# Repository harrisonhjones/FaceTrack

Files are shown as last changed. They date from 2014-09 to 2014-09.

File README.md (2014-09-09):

# FaceTrack
Banner
A visual servoing example using SimpleCV and an Arduino. 

## Motivation
The motivation behind this project came from the desire to implement visual servoing in the real world in an application I would actually use. While I don't do it often enough I occasionally video chat with my parents. When video chatting the camera position and viewport is static and usually I end up fiddling with it until it's roughly pointing at my face during the chat. If I moved around I would fall out of frame. I know some higher-end web cameras have facial tracking built into them but I never could justify the expense when it looked like something easy to implement. It turns out I was right, it's pretty easy to do!

## How It Works
This project has three core "parts". The Hardware consists of a DIY pan/tilt webcamera controlled by an arduino. The firmware simply listens for desired servo positions over the serial port and sends those to the attached servoss. The software is where the magic happens. Using a [Haar Cascade](http://simplecv.sourceforge.net/doc/cookbook.html) faces infront of the camera are recognized, facial offsets are calculated, and new servo positions are sent to the arduino over serial. The final result is a camera setup which follows your face! 

## Bill of Materials/Software
### Hardware
You need the following physical items

* A webcamera of some kind. Any usb web camera should work. I used a [Microsoft Lifecam Studio](http://www.microsoft.com/hardware/en-us/p/lifecam-studio).
* Two standard [servos](https://www.sparkfun.com/products/11884)
* Custom 3D printed pan/tilt fixture. See below for my design
* Microcontroller / Arduino. I used an Arduino Uno and my firmware is for an Uno. You may have to adapt it for your microcontroller
* Hot Glue / Adhesive Strips

### Firmware
If you are using an Arduino UNO you simply need to download the firmware (found in the "firmware" folder in the source code respository or directly [here](http://hhj.me/facetrackfirmware)) and open it using the [Arduino IDE](http://arduino.cc/en/main/software)

### Software
You need to have the following software installed

* [Python 2.7.x](https://www.python.org/download)
* [SimpleCV (A python OpenCV Wrapper)](http://simplecv.org/download)
* [pySerial](http://pyserial.sourceforge.net/pyserial.html#installation)
* A "camera splitter" if you are on Windows (perhaps other OSes as well). I've been using [ManyCam](http://manycam.com/) but I'd love to find something open source

## Running the FaceTracker
### Hardware
To get the hardware preparred for firmware and software follow the following steps.

* Assemble the custom 3D printed pan/tilt fixture. 
* Install both servos in the fixture
* Attach the servo horns to the fixtures using an adhesive. I prefer high-strengh hot glue
* Attach the fixture to your wall/monitor using an adhesive. Hot glue will work but I prefer adhesive velcro strips
* Plug the yaw servo into the Arduino. Red goes to 5V. Black goes to GND. Yellow/Brown/Signal goes to Digital Pin 9
* Plug the pitch servo into the Arduino. Red goes to 5V. Black goes to GND. Yellow/Brown/Signal goes to Digital Pin 8

### Firmware
Simply upload the Firmware.ino file to the Arduino. Open up the Serial Monitor once the upload is complete. You should see the following.

    #System Start
    $Version:1.0
    !Timeout
    !Timeout
    !Timeout
    ... (more "!Timeout")

Make a note of what serial port your arduino is on.

### Software
Open FaceTrack.py in your favorite text editor and look at for the following line

    ser = serial.Serial('COM4', 9600, timeout=1)

You want to change the serial port definition to match your setup. Change 'COM4' to match what serial port your arduino is on. 

With that change save the file and run it. If all goes well you should see your camera's viewport in a window. Once you stick your face in the view plane a red box should be drawn around it and the camera should move to bring your face toward the center of the viewport. Move around, it should follow you!

## Serial Protocol
The serial protocol is very simple. The protocol to the Arduino is fairly straight forward: ">YYYPPP\n" where YYY and PPP are zero padded numbers representing Yaw and Pitch servo positions respectively. The protocol back from the Arduino is a little more interesting. The valid formats are as follows

* #CommentGoesHere\n
* $VariableName:VariableValue\n
* !EventName\n

### Comments
Comments can be anything. They are really for debugging purposely only

### Variables
Variable names can be pretty much anything. Currently used variables are:

* Version - The firmware version number
* YawValue - The current yaw servo value
* PitchValue - The current pitch servo value

### Events
Events can be anything but only the following 3 are used/supported:

* Timeout - Indicates that the camera hasn't gotten any information for 1 second
* ACK - The last command is valid and acknowledged
* NAK - the last command is not valid

## Debugging
The biggest problems you might encounter is that every servo is different and because of that you may need to edit the software to match your setup. 

### The Camera Moves Away from my Face
If this happens you simply need to edit FaceTrack.py. Open it up and look for the following lines

    if (xErr < xErrMin):
        yawDelta = -1
    elif (xErr > xErrMax):
        yawDelta = 1
    else:
        yawDelta = 0

    if (yErr < yErrMin):
        pitchDelta = 1
    elif (yErr > yErrMax):
        pitchDelta = -1
    else:
        pitchDelta = 0

If the yaw servo is moving in the wrong direction swap the lines which read

    yawDelta = -1

and 

    yawDelta = 1

If the pitch servo is moving in the wrong direction swap the similar pitch servo lines

### The Camera "Centers" on the Wrong Spot. 
This is also an easy fix. Open up FaceTrack.py and edit the following lines near the top

    # Default positions for the yaw and pitch servos. Change these numbers to match your setup
    yawPos = 100
    pitchPos = 107

### The Camera Doesn't Move Far Enough to Either Side
Again, an easy fix. Open FaceTrack.py and edit the following lines

    if (yawPos < 30):
        yawPos = 30
    if (yawPos > 150):
        yawPos = 150
    if (pitchPos < 50):
        pitchPos = 50
    if (pitchPos > 130):
        pitchPos = 130

Change these limits to match your setup

### The Camera Oscillates or Lags Too Far Behind the Face
Open FaceTrack.py and edit the following lines

    # Tolerances. Tighter tolerances (smaller) track the face more percisel but result in move movement. If the tolerance is too small the camera might begin to oscillate.
    xErrMin = -10;
    xErrMax = 10;
    yErrMin = -10;
    yErrMax = 10;

## Custom Pan/Tilt Hardware
These part files were modeled given the following design requirements

* Mount onto a wall. The large flat on the back of the yaw servo holder is for adhesive velcro strips
* Hold two standard servos
* Semi-universally hold a web camera. Should hold onto any cylindrical or spherical camera. Made to specifically hold a Microsoft Lifecam Studio
* Be 3D printable without support material/structure. Overhangs > 45 degrees and holes not along the Z-axis should be avoided.

### Render
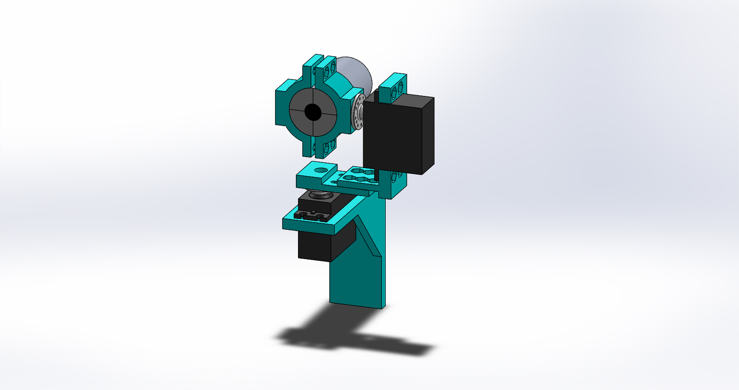
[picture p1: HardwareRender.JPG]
Render of the custom 3D printed hardware


### Model Files
Model Files can be found in the "Hardware" folder. STLs ready for 3D printing can be found in the "STLs" subfolder

## Videos/Pictures
Unfortunately I don't have any videos or pictures of this thing running. I finished this project a while back and have since needed the servos for other projects. I will try to rebuild it and take a video / pictures as soon as I find time

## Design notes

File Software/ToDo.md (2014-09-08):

#To Do

## Keyboard Commands

* Allow for tracking to be "paused" and "resumed" via keyboard (p)

* Allow for the current face to be selected via keyboard input (space for jump :P ). So, if it is currently tracking the most centered face, a spacebar press will make it jump to tracking the second face until the second face is lost and then it will track the first face

## Facial Persistance

* When given 2+ faces do not just blindly use the first face, use whatever face is closest to the last first face. Hopefully this will mitigate the persistance problem

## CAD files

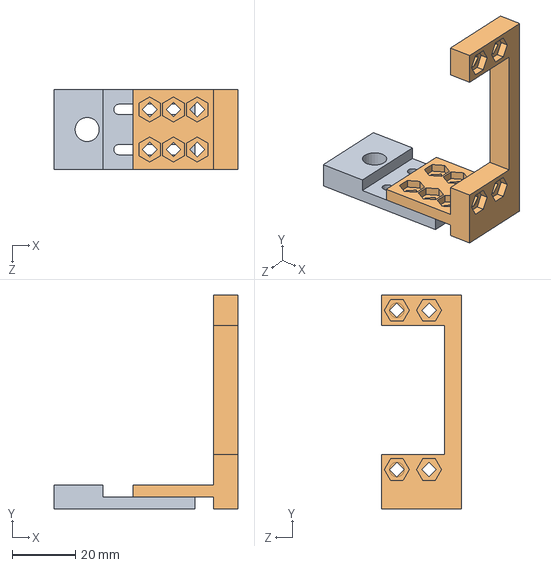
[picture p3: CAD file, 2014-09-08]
Hardware/YawArmAssembly.SLDASM
58.0 x 67.6 x 25.4 mm
YawArm-YawServoAttachment
YawArm-PitchServoAttachment

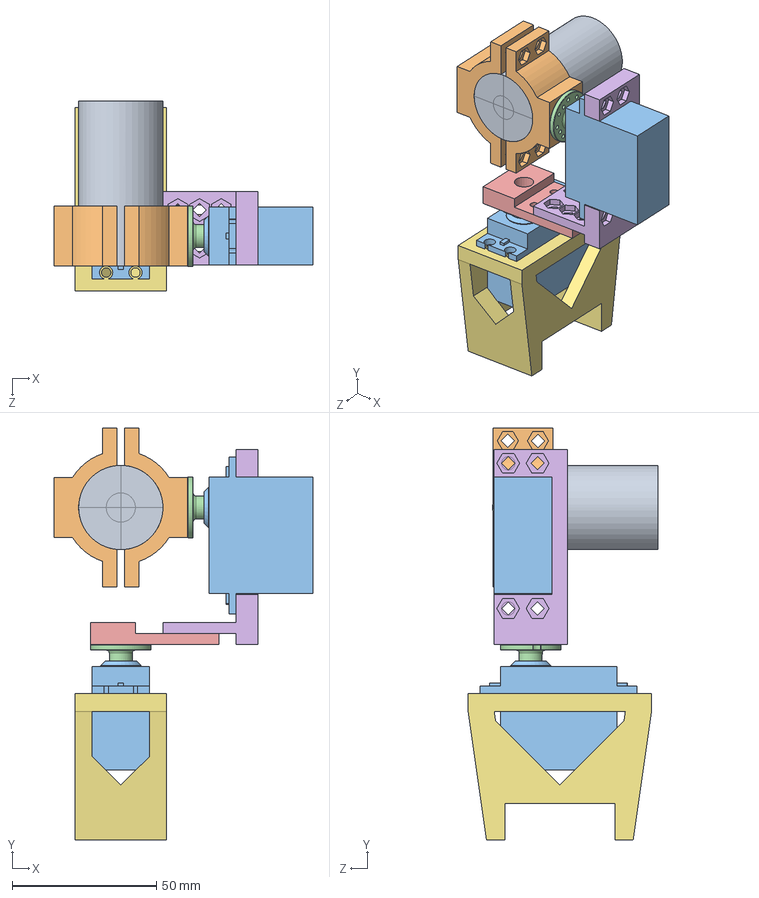
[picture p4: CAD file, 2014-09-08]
Hardware/CompleteAssembly.SLDASM
89.5 x 142.6 x 65.7 mm
Microsoft Lifecam
CameraHolder x 2
S3151 x 2
servohorn x 2
YawArm-YawServoAttachment
YawArm-PitchServoAttachment
WallPlate

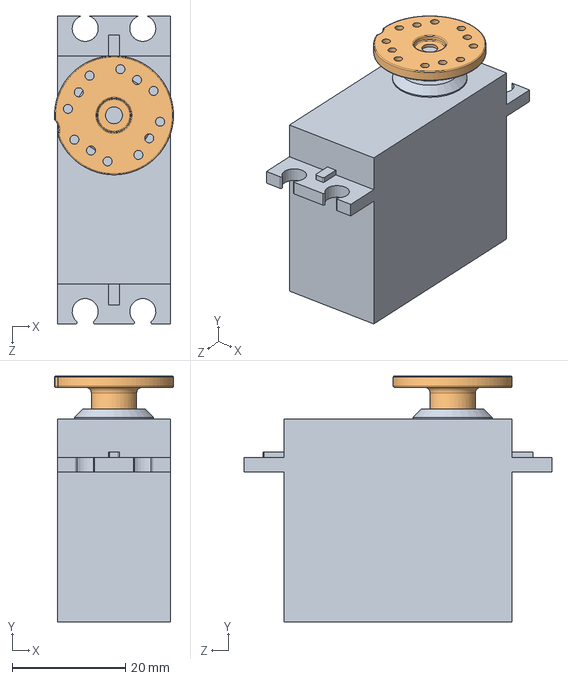
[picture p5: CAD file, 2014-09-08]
Hardware/ServoAssembly.SLDASM
21.0 x 43.4 x 54.3 mm
S3151
servohorn

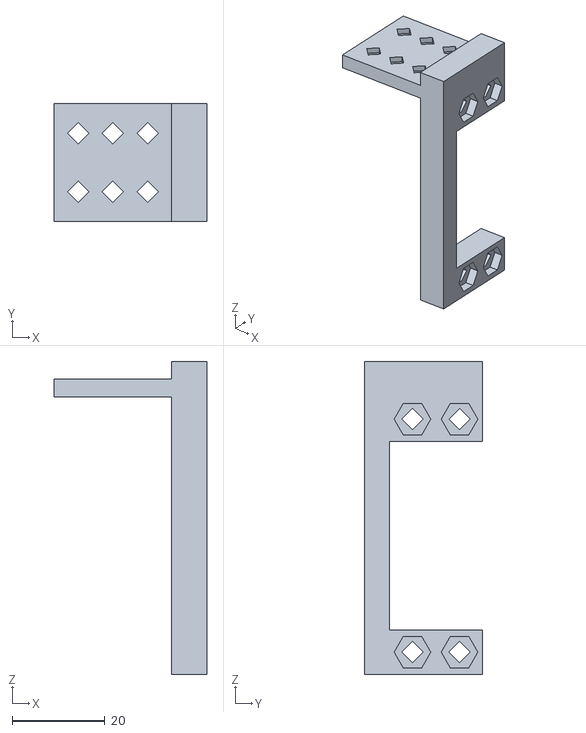
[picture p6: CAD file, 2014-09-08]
Hardware/STLs/PitchServoAttachment.STL
33.0 x 25.4 x 67.6

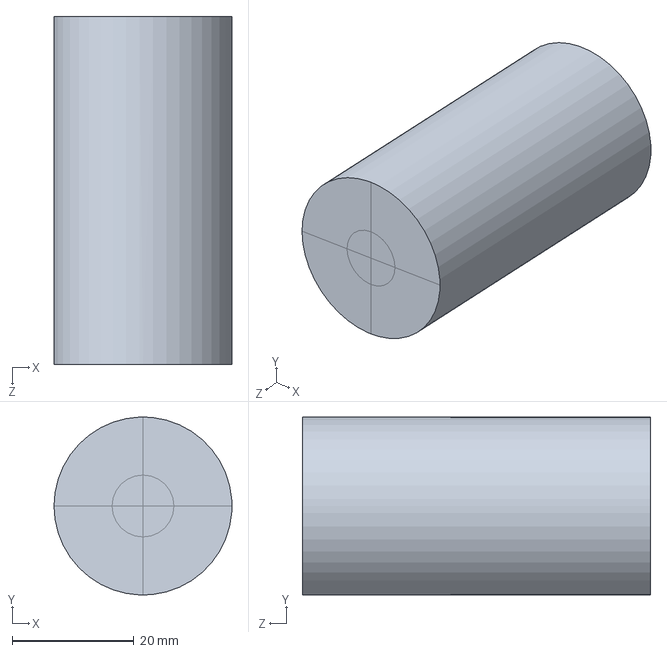
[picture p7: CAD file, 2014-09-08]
Hardware/Microsoft Lifecam.SLDPRT
29.2 x 29.2 x 57.1 mm

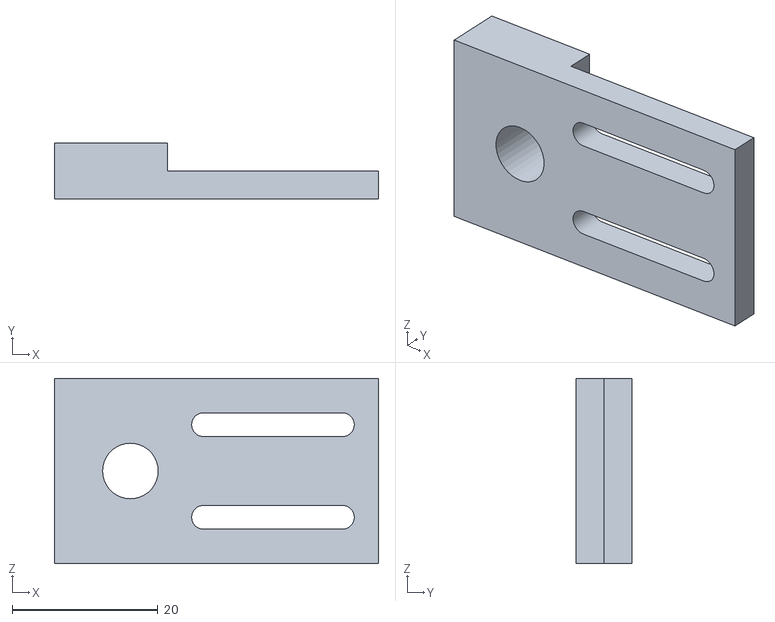
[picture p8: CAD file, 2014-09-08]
Hardware/STLs/YawServoAttachment.STL
44.5 x 7.62 x 25.4

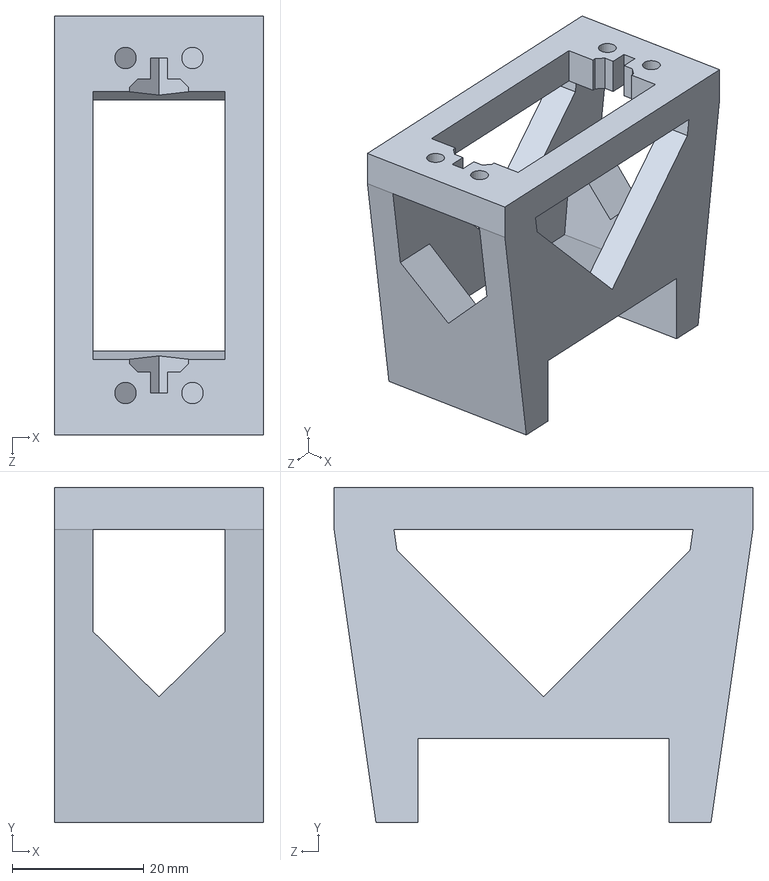
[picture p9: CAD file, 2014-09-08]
Hardware/WallPlate.SLDPRT
31.8 x 50.8 x 63.5 mm

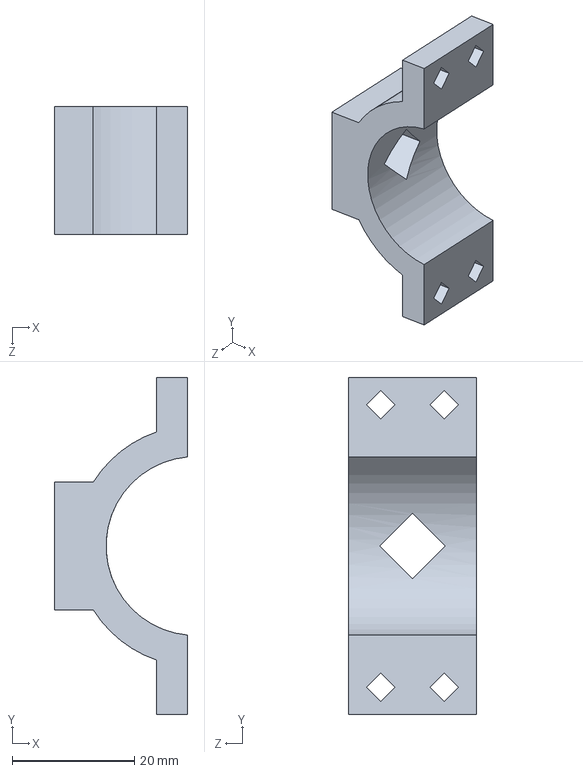
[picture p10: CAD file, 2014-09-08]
Hardware/CameraHolder.SLDPRT
21.8 x 55.0 x 20.8 mm

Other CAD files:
Hardware/YawArm-PitchServoAttachment.SLDPRT
Hardware/YawArm-YawServoAttachment.SLDPRT
Hardware/STLs/CameraHolder.STL
Hardware/STLs/WallPlate.STL

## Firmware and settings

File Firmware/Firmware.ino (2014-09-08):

// Includes
#include <Servo.h>

byte state = 0;                          // The current state. States are: 0 - waiting for start, 1-3 - waiting for yaw, 4-6 - waiting for pitch
unsigned long lastCommandTime;           // A variable to hold the last time a command was received over the serial line. Used to detect if a "timeout" has occured

String yawValue = "";                    // Two strings to hold the desired incoming (over serial) yaw and pitch values
String pitchValue = "";

Servo SRV_YAW;                          // Two servo objects. We need one for each controlled servo
Servo SRV_PITCH;

void setup() {
  Serial.begin(9600);			// opens serial port, sets data rate to 9600 bps
  
  SRV_YAW.attach(9);			// Attaches the yaw servo to pin 9
  SRV_PITCH.attach(8);			// Attaches the pitch servo to pin 10
  
  SRV_YAW.write(90);                    // Centers the yaw servo
  SRV_PITCH.write(90);                  // Centers the pitch servo
  
  Serial.println("#System Start");      // Output a comment (#) letting the user/program know the program has started
  Serial.println("$Version:1.0");       // Output a variable ($) letting the user/program know the firmware version number
}

void loop() {
  // Check for the timeout condition. If a timout has occured reset the state and let the user/program know of the event (!)
  if(millis() > lastCommandTime + 1000)
  {
    state = 0;
    Serial.println("!Timeout");
    lastCommandTime = millis();
  }
  
  // Processing incoming serial commands while we still have incoming bytes to process
  while (Serial.available() > 0) {
    lastCommandTime = millis();          // Reset the timeout clock
    int inChar = Serial.read();          // Pop a byte off of the incoming serial queue
    Serial.print("$State:");             // Debug the current state. Send it as a variable ($)
    Serial.println(state,DEC);
    if((state == 0) && (inChar == '>'))  // State the state machine. Looking for the first character ">"
    {
      state++;
    }
    else if((state > 0) && (state < 4))  // The next section of the state machine. Looking for yawValues. Builds up the yawValue string with incoming characters for later processing
    {
      yawValue += (char)inChar; 
      state++;
    }
    else if((state > 3) && (state <= 6))
    {
      pitchValue += (char)inChar; 
      state++;
    }
    else if (state > 6)                  // The end of the state machine. Outputs the yaw and pitch values and sends them to the servos
    {
      state = 0;  
      SRV_YAW.write(yawValue.toInt());                    // Send the desired yaw value to the yaw servo
      SRV_PITCH.write(pitchValue.toInt();                  // Send the desired pitch value to the pitch servo
      Serial.print("$YawValue:");
      Serial.println(yawValue.toInt());
      Serial.print("$PitchValue:");
      Serial.println(pitchValue.toInt());
      Serial.println("$Wrench");
      yawValue = "";
      pitchValue = "";
      Serial.println("!ACK");
    }
    else
    {
      state = 0;
      Serial.println("#Invalid Command Sequence");
      Serial.println("!NAK");
    }
  }
}

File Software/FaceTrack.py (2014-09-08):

'''
FaceTrack - A visual servoing example using SimpleCV and an Arduino. More info at http://hhj.me/facetrack
'''

print __doc__

import time
from SimpleCV import *
import serial, time

## OpenCV Delaration
display = Display()
cam = Camera()
# We are using a HaarCascade to detect faces
haarcascade = HaarCascade("face")

## Camera Variable Declaration
# We are talking over serial to the arduino. Change these variables to match your system
ser = serial.Serial('COM4', 9600, timeout=1)
# For some reason it takes a little time for the serial link to establish so wait 2 seconds
time.sleep(2.0)

# Default positions for the yaw and pitch servos. Change these numbers to match your setup
yawPos = 100
pitchPos = 107

# Tolerances. Tighter tolerances (smaller) track the face more percisel but result in move movement. If the tolerance is too small the camera might begin to oscillate.
xErrMin = -10;
xErrMax = 10;
yErrMin = -10;
yErrMax = 10;

# Variables used to indicate which direction to move the servos
yawDelta = 0
pitchDelta = 0

# Firmware Variables 
firmVersion = 0.0;
firmState = -1;
firmYawValue = -1;
firmPitchValue = -1;

def setVariable(rawVariableLine):
	global firmVersion, firmState, firmYawValue, firmPitchValue
	temp1 = rawVariableLine.split(':')
	if(len(temp1) == 2):
		#print "[VARIABLE] - " + temp1[0] + " = " + temp1[1]
		if(temp1[0] == "Version"):
			firmVersion = float(temp1[1])
			print "Firmware Version: " + str(firmVersion)
		elif(temp1[0] == "State"):
			firmState = int(temp1[1])
			#print "FState set"
		elif(temp1[0] == "YawValue"):
			firmYawValue = int(temp1[1])
			#print "FYawValue set"
		elif(temp1[0] == "PitchValue"):
			firmPitchValue = int(temp1[1])
			#print "FPitchValue set"
	#else:
		#print "[ERROR] - Bad Variable Length (" + str(len(temp1)) + ")"

## Helper function to send servo commands to the Arduino
def srvUpdate(yawPos, pitchPos, yawDelta, pitchDelta):
	yawPos = yawPos + yawDelta
	pitchPos = pitchPos + pitchDelta
	if (yawPos < 30):
		yawPos = 30
	if (yawPos > 150):
		yawPos = 150
	if (pitchPos < 50):
		pitchPos = 50
	if (pitchPos > 130):
		pitchPos = 130
	yawStr = str(yawPos).zfill(3)
	pitchStr = str(pitchPos).zfill(3);

	#print "[INFO] " + "> FYawValue:" + yawStr + ", FPitchValue:" + str(firmPitchValue) + ", FState:" + pitchStr

	# Custom protocol is fairly straight forward: ">YYYPPP" where YYY and PPP are zero padded numbers representing servo positions
	cmd = '>' + yawStr + pitchStr + '\n'
	ser.write(cmd)

	gotResponse = 0

	while(gotResponse == 0):
		line = ser.readline().rstrip()
		if(line[0] == "!"):
			# Got an event.
			#print "[EVENT] - " + line[1:]
			if(line[1:] == "ACK"):
				gotResponse = 1
			elif (line[1:] == "NAK"):
				gotResponse = 2
			elif (line[1:] == "Timeout"):
				gotResponse = 3
			else:
				gotResponse = -1
				print '[ERROR] - Unknown Event'
		#elif(line[0] == "#"):
			# Got an comment.
			#print "[DEBUG] - " + line[1:]
		elif(line[0] == "$"):
			# Got an variable.
			setVariable(line[1:])

	#print "[INFO] " + "< FYawValue:" + str(firmYawValue).zfill(3) + ", FPitchValue:" + str(firmPitchValue).zfill(3) + ", FState:" + str(firmState)
			
## Main Program Start
# Got to the 'home' position
srvUpdate(yawPos, pitchPos, 0, 0)

# While the display window is still open
while display.isNotDone():
	# Grab the camera image, flip it, and scale it. Scaling helps to speed up the face finding
	image = cam.getImage().flipHorizontal().scale(0.5)

	# Find the faces in the image
	faces = image.findHaarFeatures(haarcascade)

	# If there are faces, grab the first, draw a square around it, and calcualte the movement required to center the camera on it
	if faces:
		# Grab the first face. In images with more than one "face" the "first" face is not persistance and can jump between visible faces. This is one of the reasons for the yawDelta and pitchDelta variables. Instead of jumping between the two+ faces as quickly as possible, which would be hectic given the unstability of the face selection, the algorithm simply moves towards the "first" face so the final result is much smoother even with the face finding persistance problem
		face = faces[-1]
		# Draw a square around the face
		face.show(Color.RED)	

		# Calculate the error between the center of the face and the center of the camera image		 
		xErr = face.x - image.width/2
		yErr = face.y - image.height/2

		# If the error is out of tolerance set the appropriate delta so that the servo moves in the correct direction.
		if (xErr < xErrMin):
			yawDelta = -1
		elif (xErr > xErrMax):
			yawDelta = 1
		else:
			yawDelta = 0

		if (yErr < yErrMin):
			pitchDelta = 1
		elif (yErr > yErrMax):
			pitchDelta = -1
		else:
			pitchDelta = 0

	# Show the image to the user (not really necessary but interesting)
	image.show()
	# Update the servo
	srvUpdate(firmYawValue, firmPitchValue, yawDelta, pitchDelta)

# If the user closes the main window then be good citizens and close the serial connection
ser.close()
